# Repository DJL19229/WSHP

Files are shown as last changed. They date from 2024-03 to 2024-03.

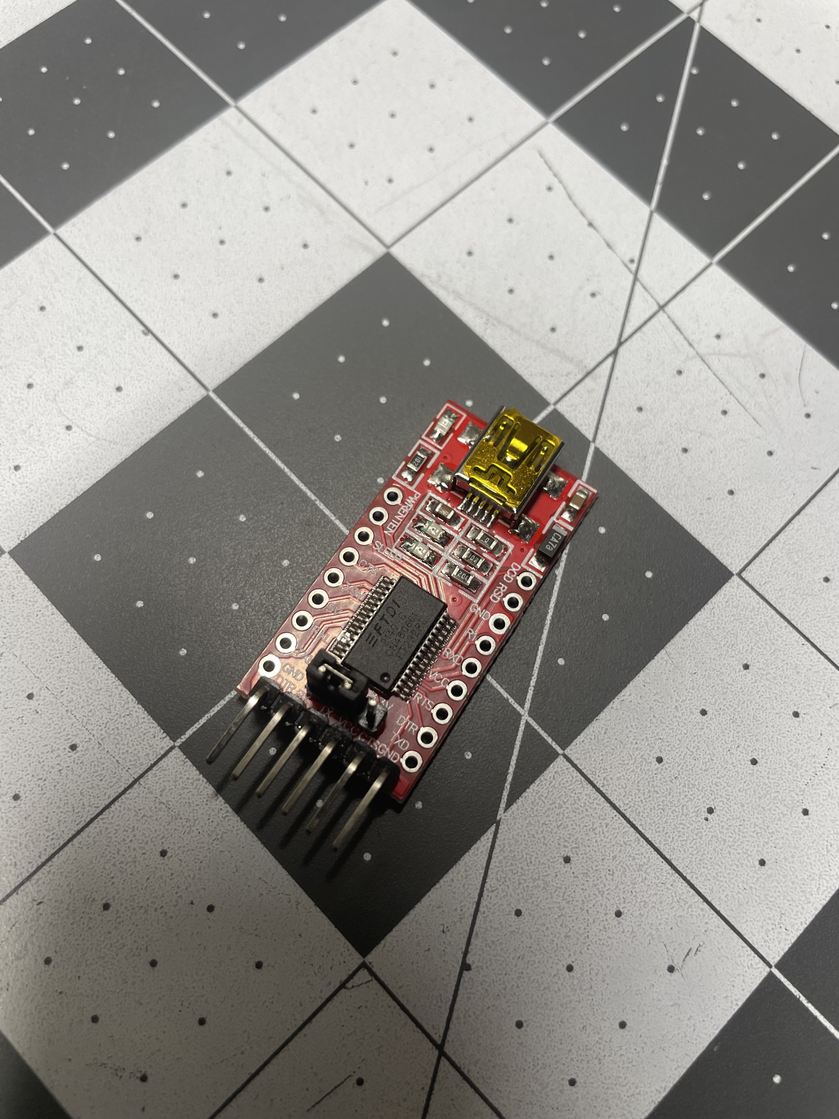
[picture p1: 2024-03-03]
IMAGES/FTDI Programmer.jpg

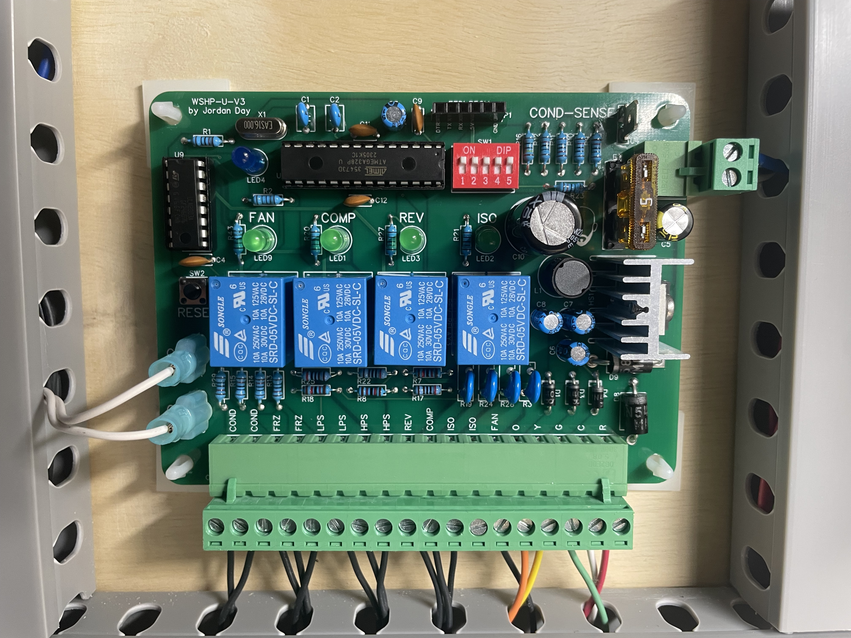
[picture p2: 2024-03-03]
IMAGES/Image 2.jpg

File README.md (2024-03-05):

# Universal Water Source Heat Pump Controller (WSHP)

This WSHP controller is an open-source project intended for facility engineers and HVAC technicians.

This repository contains:

    1) .INO file that can be uploaded to the controller with the popular Arduino IDE

    2) Wiring Diagram for a typical field application

    3) Gerber Files ready for PCB printing

    4) Bill of Materials

    5) Images of the completed project

    6) EasyEDA schematic and PCB files

Some Features of include:

    1) Error Codes via flashing LED for specific faults 
        (LPS,HPS,FRZ,COND - see bottom right corner of wiring diagram for codes).

    2) DIP switch selections for:
        -Reversing Valve Energizes in HEAT or Reversing Valve Energizes in COOL
        -Enable/Disable Freeze Protection
        -Enable/Disable Condensate Protection
        -Condensate Sensor (water sense probe) or Condensate Switch (dry contact)
        -Enable/Disable Isolation Valve Relay

    3) Small PCB Footprint

    4) Plug-type Connections (no screwdriver required to replace same board)

NOTES:

-The Wiring Diagram .QET file is editable with the free program "QElectroTech".

-The 6 pin socket allows an FTDI programmer to be plugged in directly to the board for easy programming.  
(See "FTDI Programmer" .JPG in IMAGES.)

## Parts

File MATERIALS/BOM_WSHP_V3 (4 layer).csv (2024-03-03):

ID | Name | Designator | Footprint | Quantity | Manufacturer Part | Manufacturer | Supplier | Supplier Part | Price
1 | 22pF | C1,C2 | CAP-TH_L5.5-W4.0-P5.00-D0.5 | 2 | DCH220K22YR N6FH5GD | SHM(南方宏明) | LCSC | C2896329 | 0.03
2 | 10uF | C3,C6,C7,C8 | CAP-TH_BD5.0-P2.00-D0.8-FD | 4 | ECR1HPT100MLL050011 | Nantong Jianghai Capacitor | LCSC | C190963 | 0.029
3 | 100nF | C4,C9,C11,C12 | CAP-TH_L5.0-W2.5-P5.00-D1.0 | 4 | CC1H104MC1FD3F6C10MF | Dersonic(德尔创) | LCSC | C254085 | 0.018
4 | 100uF | C5 | CAP-TH_BD8.0-P3.50-D0.6-FD | 1 | GR107M050F12RR0VH4FP0 | CX(承兴) | LCSC | C45102 | 0.028
5 | 1000uF | C10 | CAP-TH_BD13.0-P5.00-D1.2-FD | 1 | 35YXJ1000M12.5X20 | rubycon(红宝石) | LCSC | C88743 | 0.282
6 | DB2ERC-5.08-18P-GN | CN1 | CONN-TH_18P-P5.08_DB2ERC-5.08-18P-GN | 1 | DB2ERC-5.08-18P-GN | DIBO(地博电气) | LCSC | C430509 | 0.614
7 | DB2ERC-5.08-2P | CN2 | CONN-TH_2P-P5.08_DB2ERC-5.08-2P | 1 | DB2ERC-5.08-2P-GN | DIBO(地博电气) | LCSC | C395737 | 0.072
8 | SRD-05VDC-SL-C | COMP_RELAY2,FAN_RELAY1,ISO_RELAY4,REV_RELAY3 | RELAY-TH_SRD-XXVDC-XL-C | 4 | SRD-05VDC-SL-C | 松乐 | LCSC | C35449 | 0.333
9 | 1N4007_C2986225 | D1,D3,D4 | DO-41_BD2.4-L4.7-P8.70-D0.6-RD | 3 | 1N4007 | YANGJIE(扬杰) | LCSC | C2986225 | 0.026
10 | 1N5408_C698639 | D8 | DO-201AD_BD5.3-L8.4-P12.50-D1.4-RD | 1 | 1N5408 | YANGJIE(扬杰) | LCSC | C698639 | 0.106
11 | 1N5822 | D9 | DO-201AD_BD5.3-L8.4-P12.50-D1.4-FD | 1 | 1N5822 | FUXINSEMI(富芯森美) | LCSC | C3018526 | 0.064
12 | XF-507P | F1 | CONN-TH_XF-507P | 1 | XF-507P | XFCN(兴飞) | LCSC | C668119 | 0.139
13 | XSD1226-307 | HS1 | HEATSINK-TH_XSD1226-307 | 1 | XSD1226-307 | XSD(鑫顺达) | LCSC | C286232 | 0.127
14 | 100uH | L1 | IND-TH_BD10.0-P5.00-D0.7 | 1 | VLU0810-101K | FH(风华) | LCSC | C72630 | 0.092
15 | C88163 | LED1,LED2,LED3,LED9 | LED-TH_BD5.8-P2.54-L-RD | 4 | 333-2SYGD/S530-E2 | EVERLIGHT(亿光) | LCSC | C88163 | 0.034
16 | XL-502UBD | LED4 | LED-TH_BD5.9-P2.54-RD_BLUE | 1 | XL-502UBD | XINGLIGHT(成兴光) | LCSC | C2895496 | 0.024
17 | Header-Female-2.54_1x6 | P1 | HDR-TH_6P-P2.54-V-F | 1 | 2.54-1*6P母 | BOOMELE(博穆精密) | LCSC | C40877 | 0.073
18 | 10K | R1,R9,R10,R11,R12,R13,R14,R15,R23,R29 | RES-TH_BD2.2-L6.5-P10.50-D0.6 | 10 | MFR50SFTE52-10K | YAGEO(国巨) | LCSC | C173139 | 0.02
19 | 1kΩ | R2,R20,R21,R27,R43 | RES-TH_BD2.3-L6.5-P10.50-D0.5 | 5 | MF1/4W-1KΩ±1%T52 | Huaxing Mechanical-Elec. | LCSC | C713997 | 0.007
20 | 7D101K | R3,R19,R24,R28 | RES-TH_L9.0-W3.4-P5.00-D0.7-S1.50 | 4 | 7D101K | HEL(鸿志) | LCSC | C136806 | 0.029
21 | 12kΩ | R7,R8,R18 | RES-TH_BD2.2-L6.5-P10.50-D0.6 | 3 | MF1/4W-12KΩ±1% T | CCO(千志电子) | LCSC | C119349 | 0.01
22 | 1MΩ | R16 | RES-TH_BD2.3-L6.5-P10.50-D0.5 | 1 | MF1/4W-1MΩ±1%T52 | Huaxing Mechanical-Elec. | LCSC | C714052 | 0.007
23 | 2kΩ | R17,R22,R25 | RES-TH_BD2.3-L6.5-P10.50-D0.5 | 3 | MF1/4W-2KΩ±1%T52 | Huaxing Mechanical-Elec. | LCSC | C714001 | 0.007
24 | DS-05RP | SW1 | SW-TH_DS-05XP | 1 | DS-05RP | 韩国韩荣 | LCSC | C129061 | 0.364
25 | KH-6X6X4.3H-TJ | SW2 | SW-TH_4P-L6.0-W6.0-P4.50-LS6.5 | 1 | KH-6X6X4.3H-TJ | kinghelm(金航标) | LCSC | C2837514 | 0.01
26 | EST026 | U1,U4,U5 | CONN-TH_L6.3-W0.8-EST026 | 3 | EST026 | xcfuse(旭程) | LCSC | C52878 | 0.023
27 | ATMEGA328P-PU | U2 | DIP-28_L34.6-W7.3-P2.54-LS10.2-BL | 1 | ATMEGA328P-PU | MICROCHIP(美国微芯) | LCSC | C33901 | 3.914
28 | LM2576TB-5.0 | U3 | TO-220-5_L10.2-W4.8-P1.70-TL | 1 | LM2576TB-5.0 | HGSEMI(华冠) | LCSC | C5160073 | 0.619
29 | ULN2003A_C93000 | U9 | DIP-16_L20.0-W6.4-P2.54-LS7.6-BL | 1 | ULN2003A | ST(意法半导体) | LCSC | C93000 | 0.354
30 | 16MHz | X1 | OSC-TH_L10.0-W4.5-P5.00 | 1 | X49SD16MSD2SC | YXC(扬兴晶振) | LCSC | C16212 | 0.077

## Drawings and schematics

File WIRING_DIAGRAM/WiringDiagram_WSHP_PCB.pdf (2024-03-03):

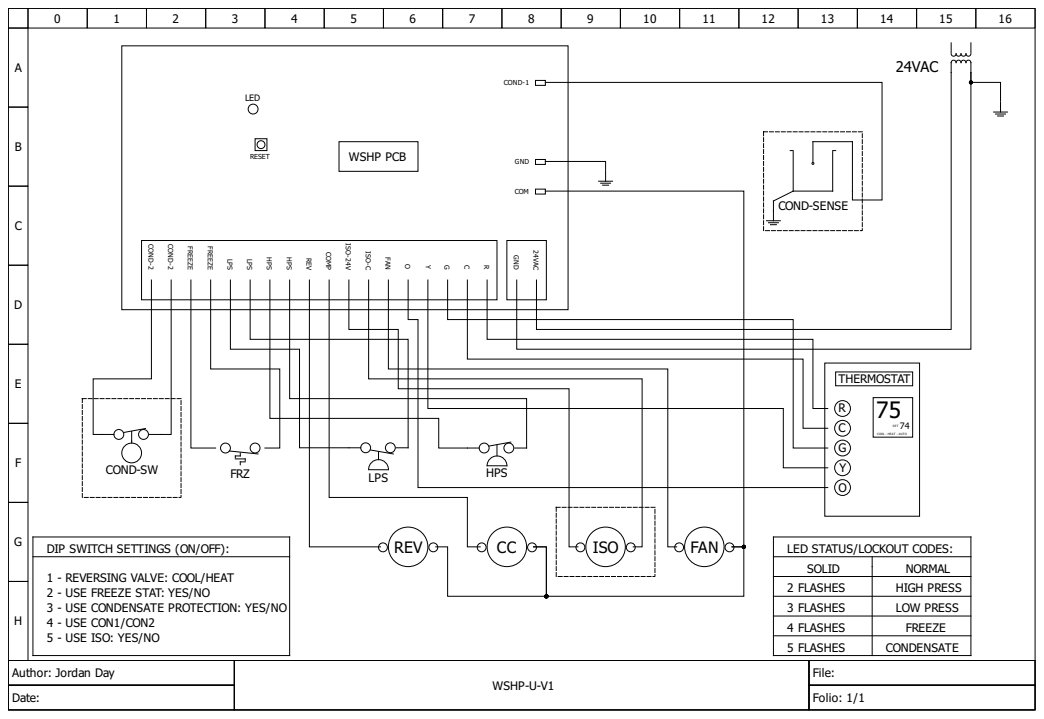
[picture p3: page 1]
WSHP-U-V1; File:; Date:; Folio: 1/1; ISO; HPS LPS; 24VAC; LPS; HPS; REV; COMP; ISO-24V; ISO-C; FREEZE; GND; FAN; COND-2; LED; RESET; WSHP PCB; COND-1; COM; COND-SENSE; SET; THERMOSTAT; SOLID; NORMAL

COOL - HEAT - AUTO

FRZ COND-SW

DIP SWITCH SETTINGS (ON/OFF):

LED STATUS/LOCKOUT CODES:

1 - REVERSING VALVE: COOL/HEAT
2 - USE FREEZE STAT: YES/NO
3 - USE CONDENSATE PROTECTION: YES/NO
4 - USE CON1/CON2
5 - USE ISO: YES/NO

2 FLASHES | HIGH PRESS
3 FLASHES | LOW PRESS
4 FLASHES | FREEZE
5 FLASHES | CONDENSATE

Author: Jordan Day

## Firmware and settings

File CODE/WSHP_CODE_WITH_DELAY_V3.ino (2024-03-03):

// C++ code

int CON1 = 0;
int HPS = 0;
int LPS = 0;
int FRZ = 0;
int SW1_REV_COOL_HEAT = 0;
int SW2_USE_FRZ_YES_NO = 0;
int SW3_USE_COND_PROT_YES_NO = 0;
int SW4_USE_CON1_CON2 = 0;
int SW5_USE_ISO_YES_NO = 0;
int FAN = 0;
int CON2 = 0;
int G5 = 0;
int Y5 = 0;
int O5 = 0;
int LED_FLASH_TIME = 0;
int counter;
int counter2;
int counter3;
int counter4;
int counter5;
int compressorInputState = LOW;       // Variable to store the state of the input pin
int previousCompressorInputState = LOW;    // Variable to store the previous state of the input pin
unsigned long previousTime = 0;   // Variable to store the previous time
unsigned long delayTime = 60000;   // COMPRESSOR TIMEOUT in milliseconds (60 seconds)
const unsigned long requiredDuration = 1000; // Fault state duration for safeties to lockout
bool delayInProgress = false;  // Flag to track delay progress

void setup()
{
  pinMode(A0, INPUT);  // Condensate Safety (1) Sensor Input
  pinMode(A1, INPUT);  // Fan Call Input
  pinMode(A2, INPUT);  // Compressor Call Input
  pinMode(A3, INPUT);  // Reversing Valve Call Input
  pinMode(A4, INPUT);  // Isolation Valve Used? (Yes or No)
  pinMode(A5, INPUT);  // Reversing Valve Engergized in ________ (Cooling or Heating)              
  pinMode(2, INPUT);   // Freeze Protection Used? (Yes or No)                                                                  
  pinMode(3, INPUT);   // Condensate Protection Used? (Yes or No)
  pinMode(4, INPUT);   // Condensate Safety Selector (1 or 2)
  pinMode(5, INPUT);   // Low Pressure Safety Switch
  pinMode(6, INPUT);   // High Pressure Safety Switch
  pinMode(7, INPUT);   // Freeze Stat Safety Switch
  pinMode(8, INPUT);   // Condensate Safety (2) Switch Input
  pinMode(9, OUTPUT);  // Isolation Valve Output
  pinMode(10, OUTPUT); // Reversing Valve Output
  pinMode(11, OUTPUT); // Compressor Output
  pinMode(12, OUTPUT); // Fan Output
  pinMode(13, OUTPUT); // Status LED

  LED_FLASH_TIME = 200; // DIAGNOSTIC LED FLASH CODE - FLASH SPEED

  delay(3000); // Startup delay for sensors to stabilize
}

void loop()
{
  // CONDENSATE SENSOR SAFETY
  CON1 = analogRead(0);
  	delay(10);
  SW3_USE_COND_PROT_YES_NO = digitalRead(3);
  	delay(10);
  SW4_USE_CON1_CON2 = digitalRead(4);
  	delay(10);
  if (SW3_USE_COND_PROT_YES_NO == HIGH && SW4_USE_CON1_CON2 == HIGH) {
    if (CON1 < 500) {
    unsigned long durationCount5 = millis();
    while (millis() - durationCount5 < requiredDuration) {
      CON1 = analogRead(0);
        delay(10);
      if (CON1 >= 500){
        break;
      }
    }
    if (CON1 < 500) {
    	if (SW3_USE_COND_PROT_YES_NO == HIGH && SW4_USE_CON1_CON2 == HIGH && CON1 < 500) {
          while (true) {
      		digitalWrite(11, LOW);
      		for (counter4 = 0; counter4 < 5; ++counter4) {
        	digitalWrite(13, LOW);
        	delay(LED_FLASH_TIME); // Wait for LED_FLASH_TIME millisecond(s)
        	digitalWrite(13, HIGH);
        	delay(LED_FLASH_TIME); // Wait for LED_FLASH_TIME millisecond(s)
        	digitalWrite(13, LOW);
        	delay(LED_FLASH_TIME); // Wait for LED_FLASH_TIME millisecond(s)
            }
           delay (3000);
           Y5 = analogRead(A2);
            delay(10);
            if (Y5 <= 500) {
              break;
            }
          	}
      	}
    }
    }      
  }
   else {
    digitalWrite(13, HIGH);
   }
  
  
  // CONDENSATE SWITCH SAFETY
  CON2 = digitalRead(8);
  	delay(10);
  SW3_USE_COND_PROT_YES_NO = digitalRead(3);
  	delay(10);
  SW4_USE_CON1_CON2 = digitalRead(4);
  	delay(10);
  if (SW3_USE_COND_PROT_YES_NO == HIGH && SW4_USE_CON1_CON2 == LOW) {
    if (CON2 == LOW) {
    unsigned long durationCount4 = millis();
    while (millis() - durationCount4 < requiredDuration) {
      CON2 = digitalRead(8);
      delay(10);
      if (CON2 == HIGH) {
        break;
      }
    }
    if (CON2 == LOW) {
    	if (CON2 == LOW) {
          while (true) {
      		digitalWrite(11, LOW);
      		for (counter4 = 0; counter4 < 5; ++counter4) {
        	digitalWrite(13, LOW);
        	delay(LED_FLASH_TIME); // Wait for LED_FLASH_TIME millisecond(s)
        	digitalWrite(13, HIGH);
        	delay(LED_FLASH_TIME); // Wait for LED_FLASH_TIME millisecond(s)
        	digitalWrite(13, LOW);
        	delay(LED_FLASH_TIME); // Wait for LED_FLASH_TIME millisecond(s)
            }
           delay (3000);
           Y5 = analogRead(A2);
            delay(10);
            if (Y5 <= 500) {
              break;
            }
          	}
      	}
    }
    }      
  }
   else {
    digitalWrite(13, HIGH);
   }
  
  
  // HIGH PRESSURE SWITCH SAFETY
  HPS = digitalRead(6);
  	delay(10);
  if (HPS == LOW) {
    unsigned long durationCount2 = millis();
    while (millis() - durationCount2 < requiredDuration) {
      HPS = digitalRead(6);
        delay(10);
      if (HPS == HIGH) {
        break;
      }
    }
    if (HPS == LOW) {
    	if (HPS == LOW) {
          while (true) {
      		digitalWrite(11, LOW);
      		for (counter4 = 0; counter4 < 2; ++counter4) {
        	digitalWrite(13, LOW);
        	delay(LED_FLASH_TIME); // Wait for LED_FLASH_TIME millisecond(s)
        	digitalWrite(13, HIGH);
        	delay(LED_FLASH_TIME); // Wait for LED_FLASH_TIME millisecond(s)
        	digitalWrite(13, LOW);
        	delay(LED_FLASH_TIME); // Wait for LED_FLASH_TIME millisecond(s)
            }
           delay (3000);
           Y5 = analogRead(A2);
            delay(10);
            if (Y5 <= 500) {
              break;
            }
          	}
      	}
    }      
  }
   else {
    digitalWrite(13, HIGH);
   }
  
  
  // LOW PRESSURE SWITCH SAFETY
  LPS = digitalRead(5);
  	delay(10);
  if (LPS == LOW) {
    unsigned long durationCount = millis();
    while (millis() - durationCount < requiredDuration) {
      LPS = digitalRead(5);
        delay(10);
      if (LPS == HIGH) {
        break;
      }
    }  
    if (LPS == LOW) {
      if (LPS == LOW) {
          while (true) {
      		digitalWrite(11, LOW);
      		for (counter4 = 0; counter4 < 3; ++counter4) {
        	digitalWrite(13, LOW);
        	delay(LED_FLASH_TIME); // Wait for LED_FLASH_TIME millisecond(s)
        	digitalWrite(13, HIGH);
        	delay(LED_FLASH_TIME); // Wait for LED_FLASH_TIME millisecond(s)
        	digitalWrite(13, LOW);
        	delay(LED_FLASH_TIME); // Wait for LED_FLASH_TIME millisecond(s)
            }
           delay (3000);
           Y5 = analogRead(A2);
            delay(10);
            if (Y5 <= 500) {
              break;
            }
          	}
      	}
    }      
  }
   else {
    digitalWrite(13, HIGH);
  }
  
  
  // FREEZE PROTECTION SWITCH SAFETY
  FRZ = digitalRead(7);
  	delay(10);
  SW2_USE_FRZ_YES_NO = digitalRead(2);
    delay(10);
  if (SW2_USE_FRZ_YES_NO == HIGH && FRZ == LOW) {
    unsigned long durationCount3 = millis();
    while (millis() - durationCount3 < requiredDuration) {
      FRZ = digitalRead(7);
        delay(10);
      if (FRZ == HIGH) {
        break;
      }
    }
    if (FRZ == LOW) {
    	if (FRZ == LOW) {
          while (true) {
      		digitalWrite(11, LOW);
      		for (counter4 = 0; counter4 < 4; ++counter4) {
        	digitalWrite(13, LOW);
        	delay(LED_FLASH_TIME); // Wait for LED_FLASH_TIME millisecond(s)
        	digitalWrite(13, HIGH);
        	delay(LED_FLASH_TIME); // Wait for LED_FLASH_TIME millisecond(s)
        	digitalWrite(13, LOW);
        	delay(LED_FLASH_TIME); // Wait for LED_FLASH_TIME millisecond(s)
            }
           delay (3000);
           Y5 = analogRead(A2);
            delay(10);
            if (Y5 <= 500) {
              break;
            }
          	}
      	}
    }      
  }
   else {
    digitalWrite(13, HIGH);
   }
  
  
  // FAN CALL
  G5 = analogRead(A1);
  	delay(10);
  if (G5 > 500) {
    digitalWrite(12, HIGH);
    delay(10); // Wait for 10 millisecond(s)
  } else {
    digitalWrite(12, LOW);
    delay(10); // Wait for 10 millisecond(s)
  }
  
  
  // ISOLATION VALVE CALL
  SW5_USE_ISO_YES_NO = analogRead(A4);
  	delay(10);
  Y5 = analogRead(A2);
    delay(10);
  if (SW5_USE_ISO_YES_NO > 500 && Y5 > 500) {
    digitalWrite(9, HIGH);
    delay(10); // Wait for 10 millisecond(s)
  } else {
    digitalWrite(9, LOW);
    delay(10); // Wait for 10 millisecond(s)
  }
  
  
  // COMPRESSOR CALL
  Y5 = analogRead(A2);
  	delay(10);
  if (Y5 > 500) {
    compressorInputState = HIGH;
  }
  if (Y5 <= 500) {
    compressorInputState = LOW;
  }

  if (compressorInputState == HIGH && previousCompressorInputState == LOW) {
    // Input state transitioned from LOW to HIGH
    previousTime = millis();  // Record the current time
    delayInProgress = true;
  }

  if (delayInProgress && (millis() - previousTime >= delayTime)) {
    // Delay completed
    digitalWrite(11, HIGH);
    delayInProgress = false;
  }

  if (compressorInputState == LOW) {
    // Input state is LOW, turn off the output immediately
    digitalWrite(11, LOW);
    delayInProgress = false;
  }

  previousCompressorInputState = compressorInputState;
  
  
  // REVERSING VALVE CALL (ENERGIZING IN COOL)
  SW1_REV_COOL_HEAT = analogRead(A5);
  	delay(10);
  O5 = analogRead(A3);
  	delay(10);
  if (SW1_REV_COOL_HEAT > 500) {
    O5 = analogRead(A3);
  	delay(10);
    if (O5 > 500) {
      digitalWrite(10, HIGH);
      delay(10); // Wait for 10 millisecond(s)
    } else {
      digitalWrite(10, LOW);
      delay(10); // Wait for 10 millisecond(s)
    }
  }
  

  // REVERSING VALVE CALL (ENERGIZING IN HEAT)
  SW1_REV_COOL_HEAT = analogRead(A5);
  	delay(10);
  O5 = analogRead(A3);
  	delay(10);
  if (SW1_REV_COOL_HEAT <= 500){
    Y5 = analogRead(A2);
  	delay(10);
    if (Y5 <= 500 && O5 <= 500){
      digitalWrite(10, LOW);
      delay(10);
    }
  }
  
  if (SW1_REV_COOL_HEAT <= 500) {
    Y5 = analogRead(A2);
  	delay(10);
    if (Y5 > 500 && O5 > 500) {
      digitalWrite(10, LOW);
      delay(10); // Wait for 10 millisecond(s)
    }
  }
  
  if (SW1_REV_COOL_HEAT <= 500) {
    Y5 = analogRead(A2);
  	delay(10);
    if (Y5 <= 500 && O5 > 500) {  
      digitalWrite(10, LOW);
      delay(10); // Wait for 10 millisecond(s)
    }
  }
  
  if (SW1_REV_COOL_HEAT <= 500) {
    Y5 = analogRead(A2);
  	delay(10);
    if (Y5 > 500 && O5 <= 500) {
      digitalWrite(10, HIGH);
      delay(10); //Wait for 10 millisecond(s)
    }
  }
  
  delay(10); // Wait for 10 millisecond(s)
}

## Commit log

2024-03-03 Rename BOM_WSHP_V3 (4 layer).csv to MATERIALS/BOM_WSHP_V3 (4 layer).csv
    [BOM_WSHP_V3 (4 layer).csv]
2024-03-05 Rename 1-Schematic_WSHP Control V3.json to EasyEDA/1-Schematic_WSHP Control V3.json
2024-03-05 Rename 2-PCB_PCB_WSHP Control V3 (4 layer).json to EasyEDA/2-PCB_PCB_WSHP Control V3 (4 layer).json
